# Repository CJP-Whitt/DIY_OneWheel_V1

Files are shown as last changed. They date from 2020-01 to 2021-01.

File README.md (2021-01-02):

# DIY OneWheel
Custom DIY OneWheel Electric Board. I decided to try to make an easy to follow guide on my one wheel process in hopes that everyone else doesn't have to go through the same pain as me in order to do their own DIY OneWheel. Very fun project with great opportunities for learning to engineer.

Link to the CAD File --> https://a360.co/2GcbuvP

# Disclaimer!
Do your research! I do not take responsibility for any issues you may encounter during your build if you attempt to make a onewheel. It is difficult and there are many roadblocks you must engineer your way through. Learning comes through failure and troubleshooting so get used to it now if you plan on doing more projects in the future.

# Finished Project
### _Max Range: 5.5 miles (8.8 km), Max Speed: 20mph (32 kmh)_
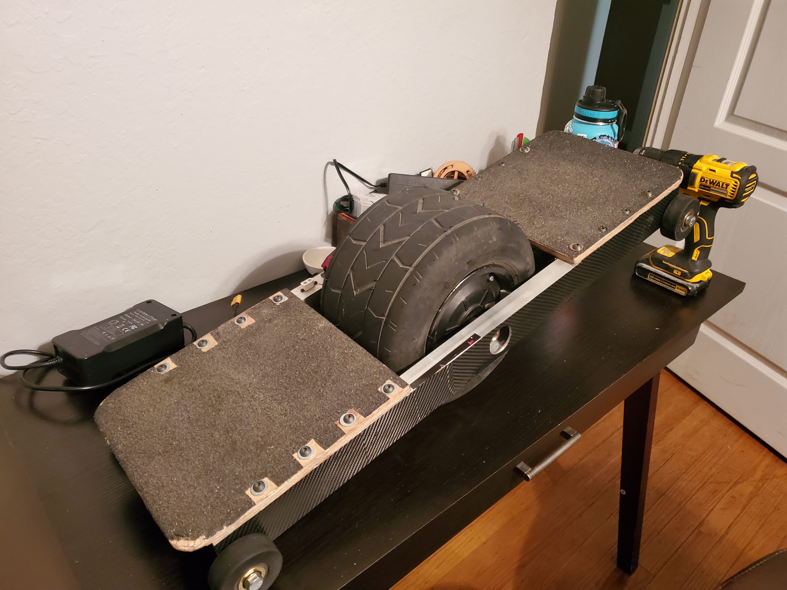
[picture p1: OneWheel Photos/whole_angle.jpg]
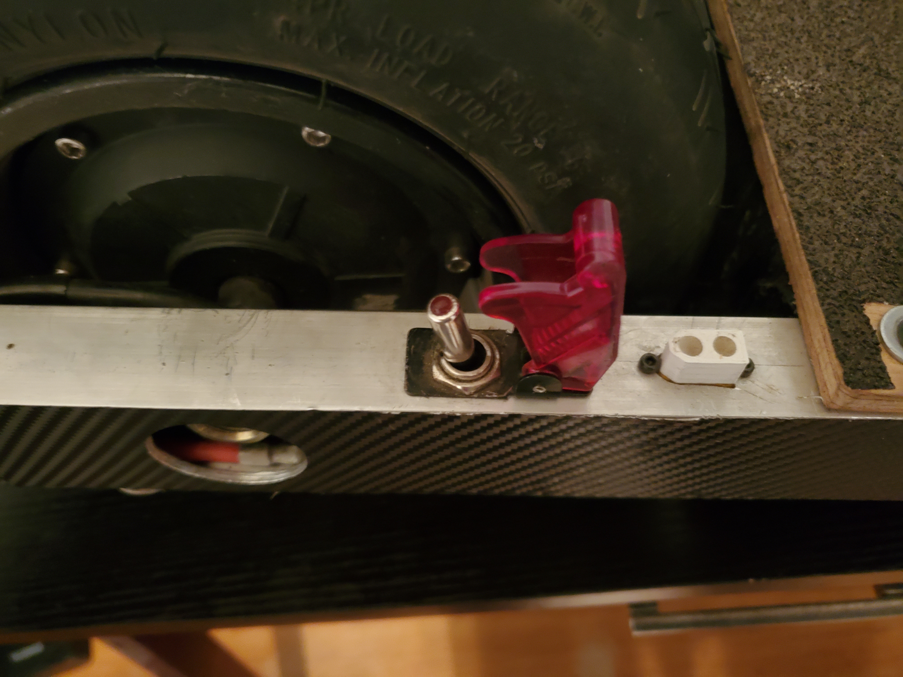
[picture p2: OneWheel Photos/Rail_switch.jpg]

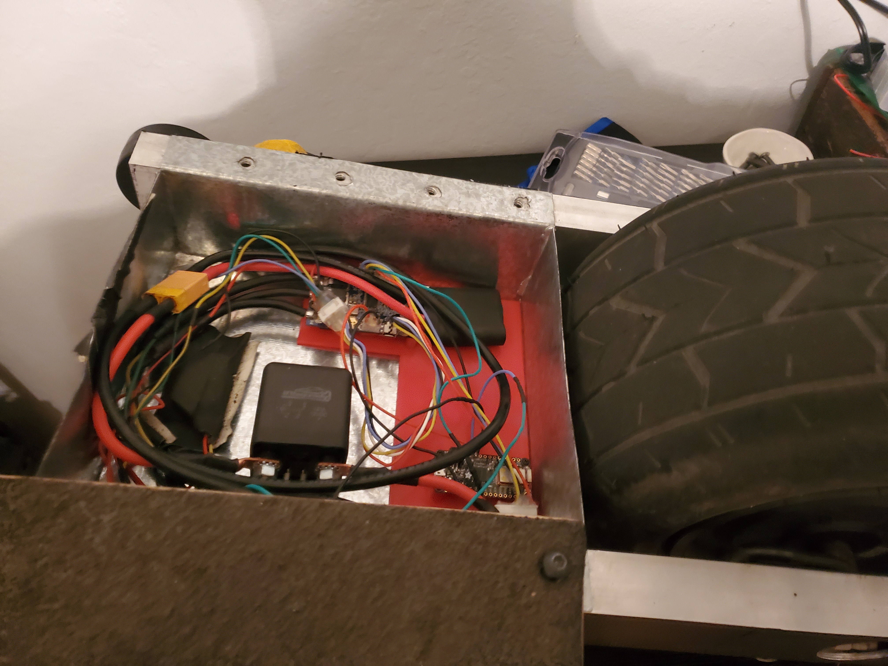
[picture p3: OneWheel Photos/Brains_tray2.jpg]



# Components
**Fundamental Components**
1. MPU6050 gyro, you can get these anywhere.
2. TORQUE ESC BLDC ELECTRONIC SPEED CONTROLLER (VESC-Motor Controller): https://diyelectricskateboard.com/products/torque-esc-bldc-electronic-speed-controller
3. 10inch 10 inch 10x6.00-5.5 wide tubeless tyre brushless gearless dc wheel hub motor (600W, 48V): https://www.aliexpress.com/item/32823573279.html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,searchweb201602_10,searchweb201603_55
4. Grip Tape (Get this anywhere that fits and has good reviews)
5. 13 18650 3.7 single cell batteries: (Get this anywhere, preferably samsung brand)
6. 48V 13s Battery Management System (BMS): https://vruzend.com/product/48v-13s-battery-management-system-bms/
7. VRUZEND battery kit V2.1 (Battery Clips): https://vruzend.com/product/vruzend-battery-kit-v2-0/
8. Relay 12v switch, 120A max (really only needs to be more Amps rating than your fuse by a little): https://www.amazon.com/Heavy-Duty-Relay-Split-Charge/dp/B07T35K8S2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
9. 60v to 3v-32v step-down converter, preferably one with a flyback diode, you can get them everywhere and I got one on ebay

**Other Components**
1. Pressure-Sensitive Conductive Sheet: https://www.adafruit.com/product/1361
2. Aluminum Rectangular Hollow Tube 2" x 1" https://store.buymetal.com/aluminum/rectangular-tube/6061-t6-t6511/aluminum-rectangular-tube-6061-t6511-2-1-0.125.html
3. Switch, I used an aircraft style switch because they look cool...but any will work as long as it works with the output voltage of your voltage step-down converter. In my case it was 12v
4. If you are doing the arduino method you need another voltage step-down from 48ish volts to 5v to power your arduino board
5. I suggest using JST Connectors!!! It's super cheap to get on Amazon and will help you undo your mistakes much easier
6. Rubber wheels with bearing: https://www.mcmaster.com/catalog/126/1524

# Build Info
- 48v 13s 2p Battery Pack
- (Easy) Vesc open source balancing tool
- (Hard) Arduino self made balancing logic

# Build Progression

### Step One: The frame
I have created a CAD file (Uses Fusion 360 which is FREE!) for the frame if you want to follow my process, but generally you need two rails that will hold the wires going from the battery compartment to your other component and mounts for connecting the motor axle to your rails. If you are a machinist this will be fairly easy, but if not I suggest you have someone else do this part. My CAD files provide the general outline but you need to decide how you want to do your own motor mounts. The third pic is after I finished and put my switch and stuff in. The yellow male connector is wired for charging to the bms and pack.
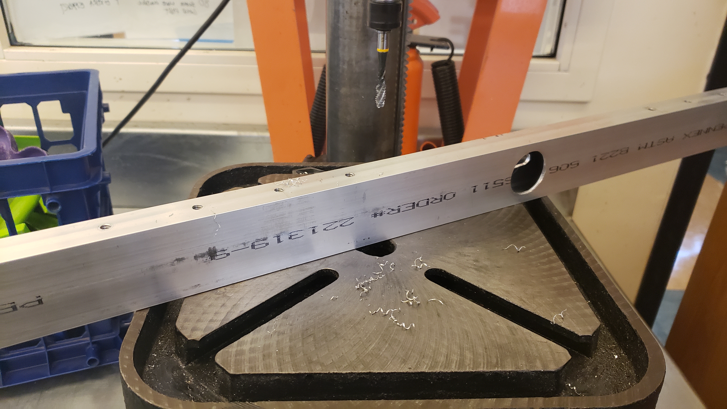
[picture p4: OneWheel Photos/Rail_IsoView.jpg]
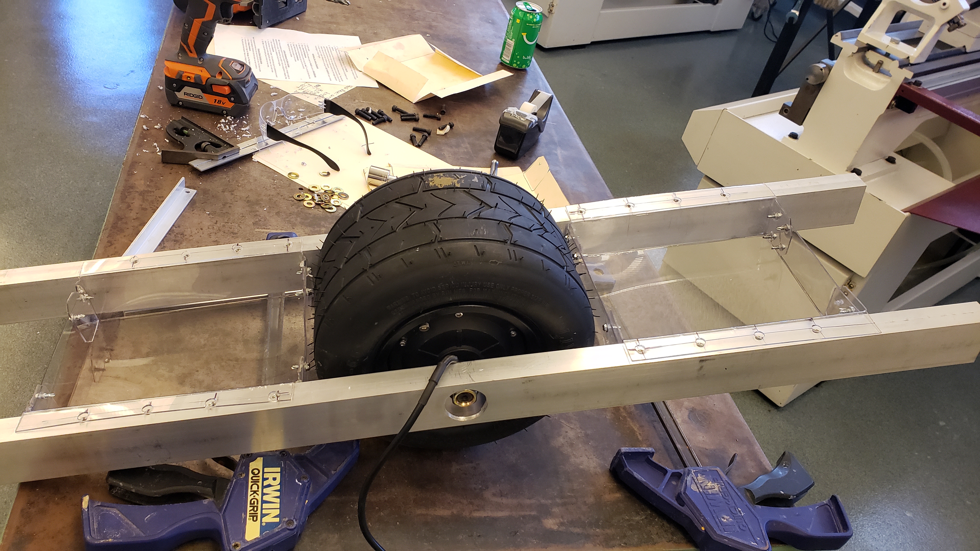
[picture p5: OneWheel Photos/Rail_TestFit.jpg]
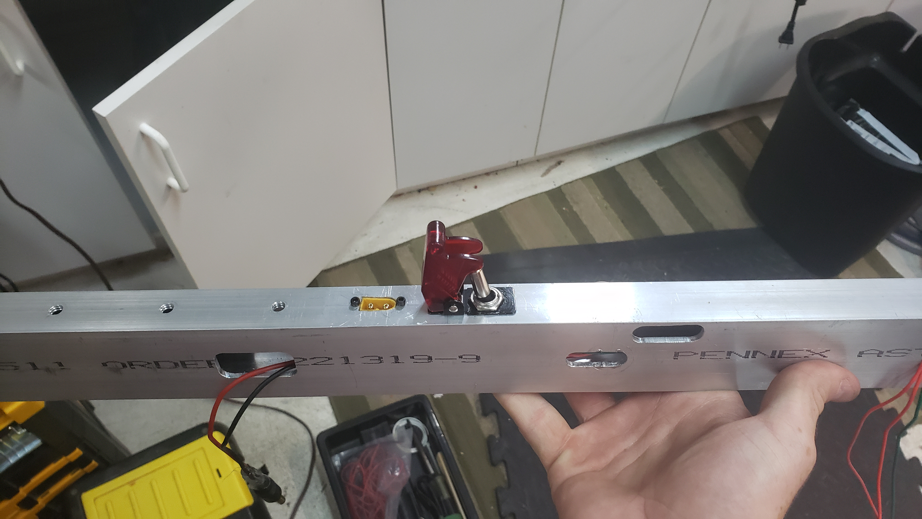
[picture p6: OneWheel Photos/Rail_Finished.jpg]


- Two rails
- Motor mounts: I attached straight to rails with a slot lock washer that comes with the wheel. Did not hold up very long : ( 
- Holes on top of rails to attach component trays and foot pads
- I would suggest getting the rails extra long just in case you need larger component trays than you first thought, you can cut them later

The Aluminum was too weak to support the motor axle twisting back and forth constantly so I made some L shaped steel brackets with a slot in the middle for the axle. I don't have any pics of them when I was working on them but here you can see them on the rails.
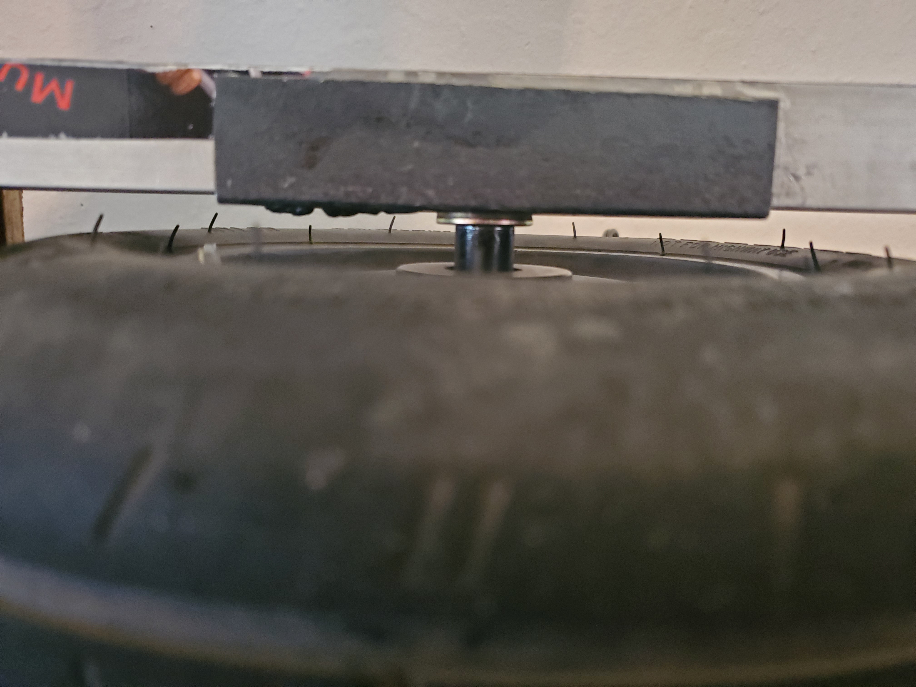
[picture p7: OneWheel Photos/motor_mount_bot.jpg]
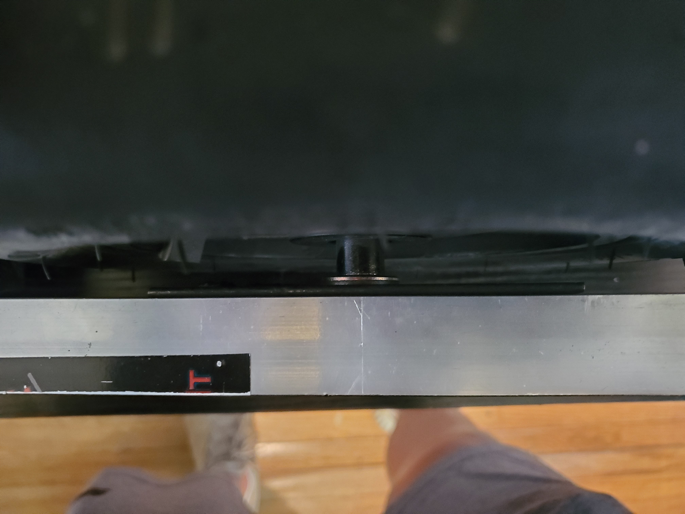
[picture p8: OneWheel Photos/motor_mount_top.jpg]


### Step Two: Battery Pack
I would suggest that if you are unfamiliar with batteries you do some research prior to building your packs. Essentially I built two 13 cell packs and ran them parallel, but it's not apparent from my final photo because I did some wiring magic to make more space in my battery tray.
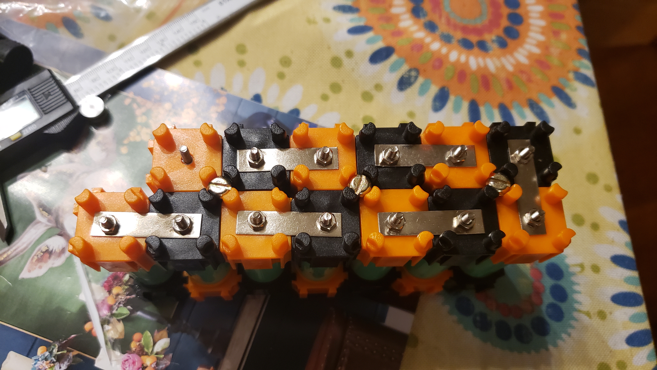
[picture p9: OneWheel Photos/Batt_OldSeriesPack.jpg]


- 26 18650 3.7 cells total
- 13 cells in series (x2)
- Put both those packs in parallel
- (You could do this with 13 cells and just make one pack if you really want, it will have the same voltage, but I wanted more amp-hours)
- Look at the wiring guide for your battery management system (BMS) and wire accordingly. In my case I soldered 1 balancing wire to each two cell groups for a total of 13 wires. Then I connected the + and - wires to their respective locations. This video helped me a lot: https://www.youtube.com/watch?v=m4DGDkwFr54

### Step Three: Component Wiring
At this point in the project I 3D printed two trays to hold my batteries and components. I also printed a plate to hold all of my non battery components, all these components are in the OneWheel frame CAD file.
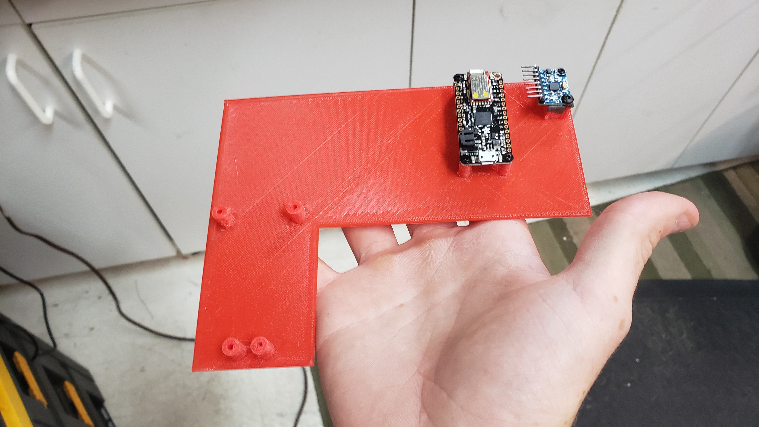
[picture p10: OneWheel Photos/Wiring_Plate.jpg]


Here is a general wiring diagram for the OneWheel. Sorry for how unprofessional it is. Keep in mind if you are using something besides the VESC balancing app you need to wire the arduino board or whatever you use for the balancing logic in between the vesc and relay.
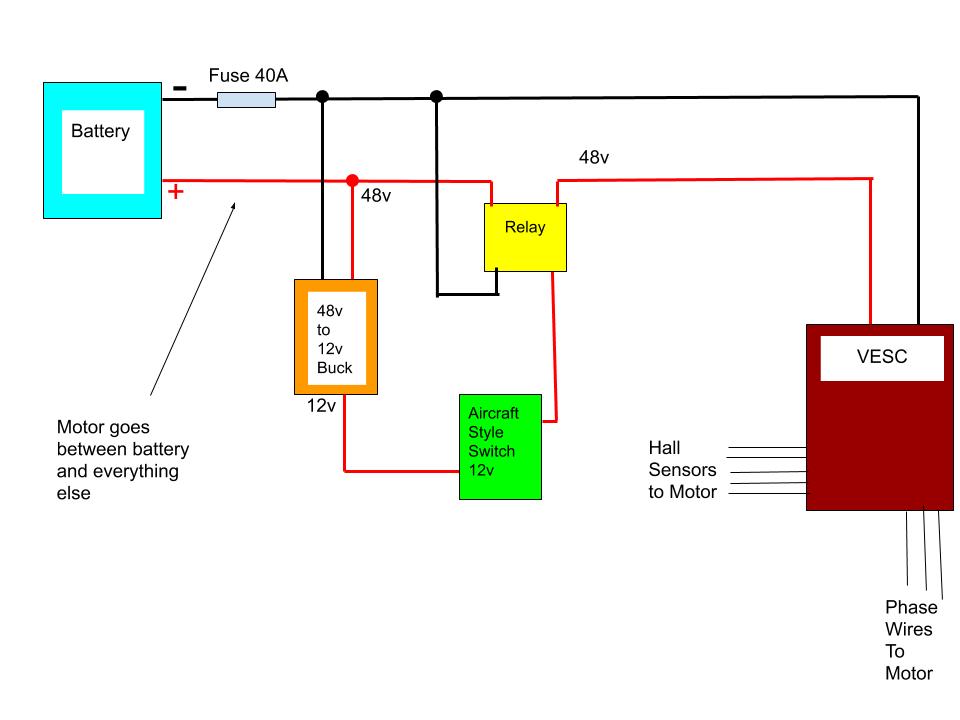
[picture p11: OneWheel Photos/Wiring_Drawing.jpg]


This is the adjustable voltage step down converter I used
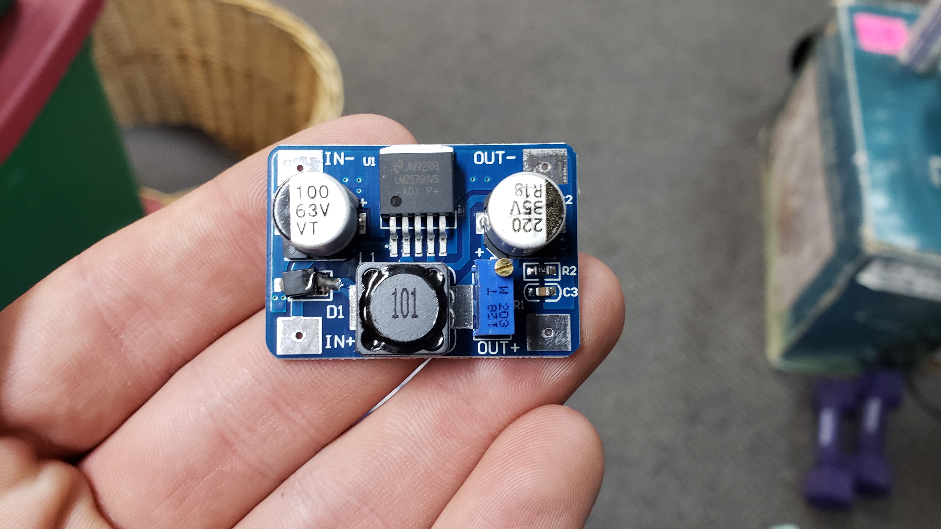
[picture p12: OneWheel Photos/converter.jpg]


Here is a photo of the hall sensor connection to the VESC, from left to right in the pic it goes 5v,Temp,H3,H2,H1,GND
I'm pretty sure the order of hall sensors doesn't matter, if it doesn't work in vesc than just switch two and it should.
Same goes for the phase wires (The 3 bullet connectors coming from the motor).
The motor listed in the parts section does not have a temp wire so leave that pin empty.
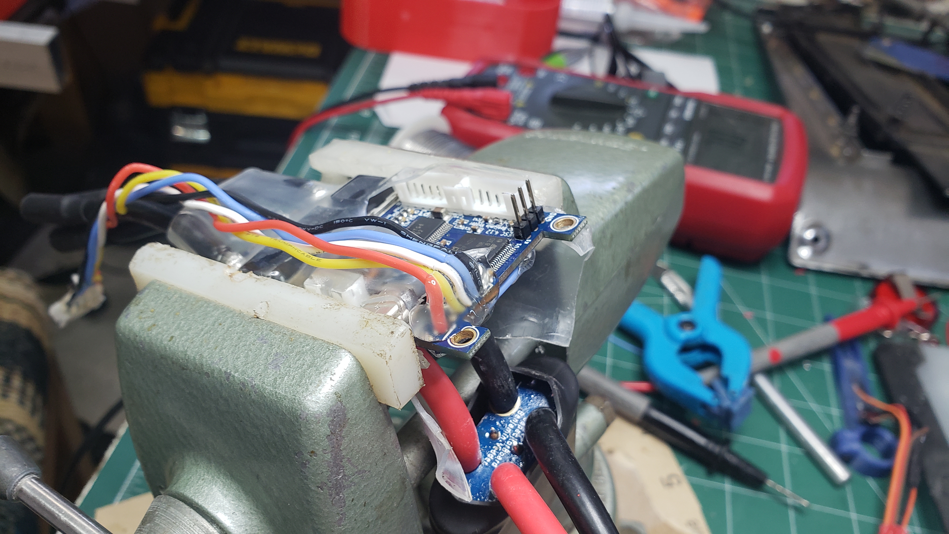
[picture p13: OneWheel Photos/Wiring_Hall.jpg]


This is the wiring for the MPU6050...
alt test

And its connection to the VESC, it's the connector at the front of the picture.
The wires you don't see in the MPU (Dark Blue, two greens) are the wires for the switches, which will be wired to footpads later, but it's best to just use them as bare wires for testing. Dark blue is the 3.3v pin, and when connected with one or both green wires (MISO, SCK) it will toggle switches on the VESC we will use later.
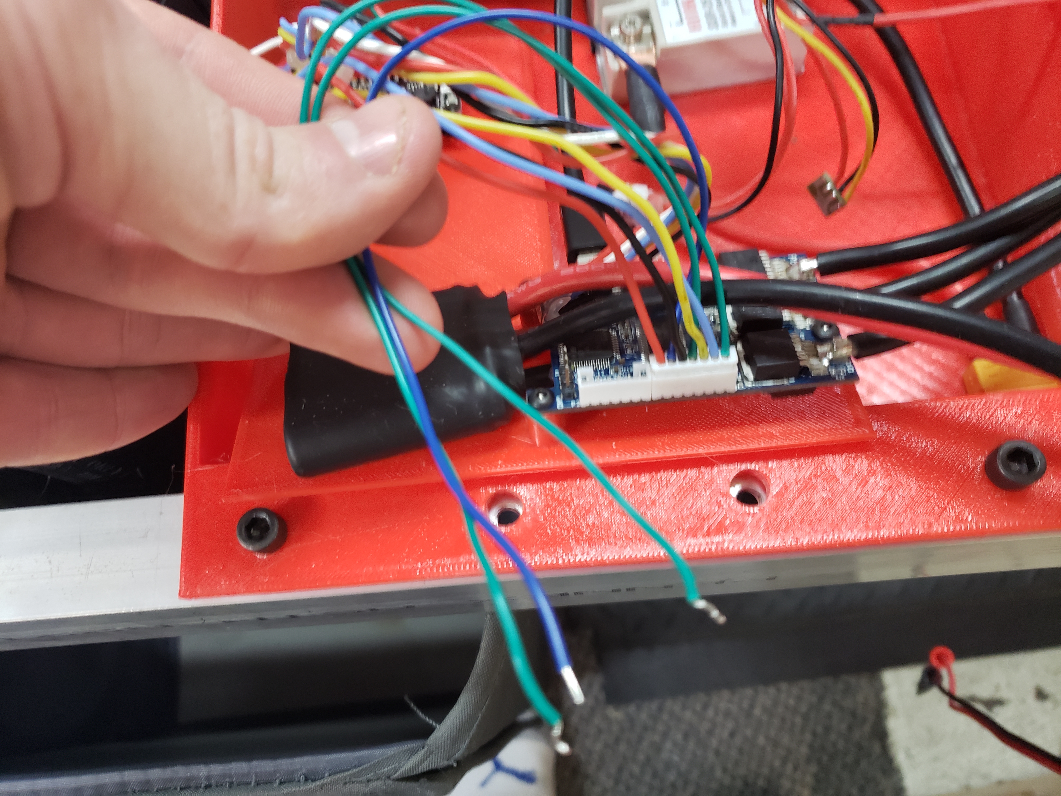
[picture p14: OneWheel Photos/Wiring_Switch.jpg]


#### Finished Component and Battery Tray
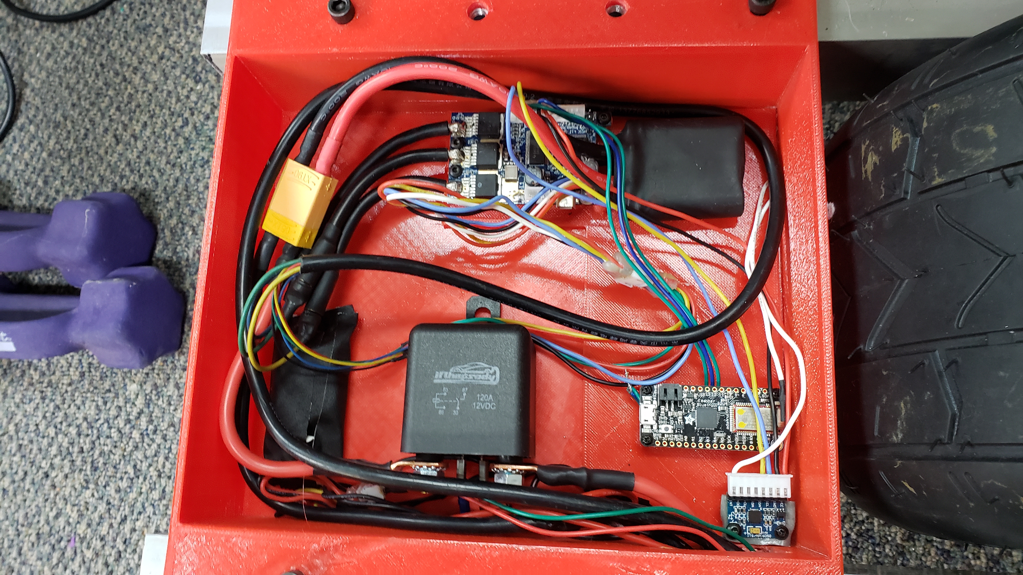
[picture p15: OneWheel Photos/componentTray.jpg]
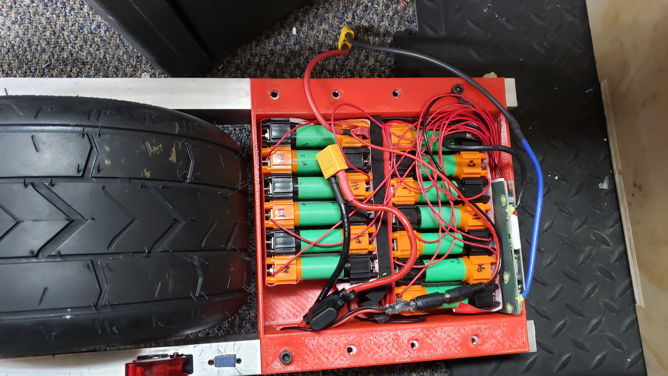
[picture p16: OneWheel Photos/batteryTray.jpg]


### Step Four: Metal Trays
The 3D printed trays were not holding up in early tests so I made some metal trays out of very thin steel sheet metal.
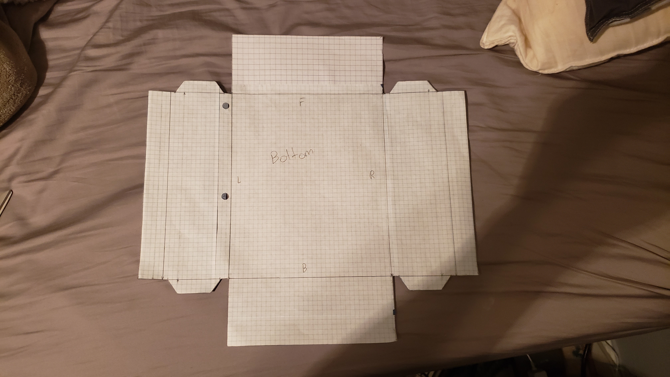
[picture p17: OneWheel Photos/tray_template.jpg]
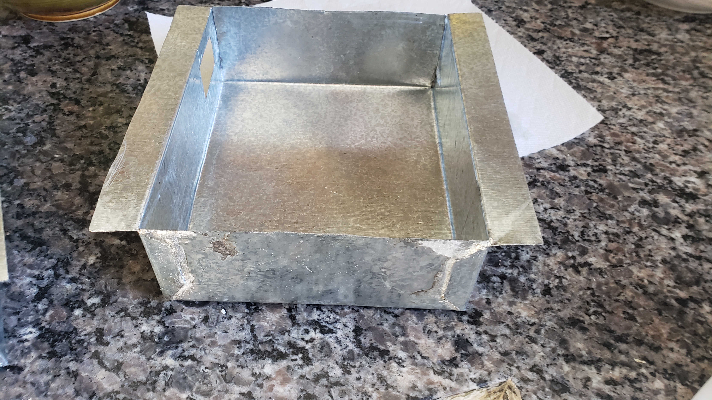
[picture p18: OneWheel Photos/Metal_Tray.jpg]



### Step Five: VESC App
With everything now wired up I would suggest you test using a multimeter from the beginning of your wiring to the end to make sure you don't fry anything. This is also why I say to use a fuse.

Plug in your vesc and open the app (Google how to get the app, it's easy). Then turn on your OneWheel
Here is a good video on how to set it all up: https://www.youtube.com/watch?v=0y5ME2SgwLg

I have XML files for the settings of the motor and app configuration in this repo

After this you can technically ride it fairly easily but it will only go 12mph so I went ahead and added some other stuff to make the ride better.

### Safety Wheels
I bought some rubber wheels with bearings from McMaster-Carr but sadly I measured something wrong and they didn't fit inside the rails, so I attached them on the outer side of the rail, with the bolt going through a hole on the other side for rigidity.

Here they are attached to the side of the rails
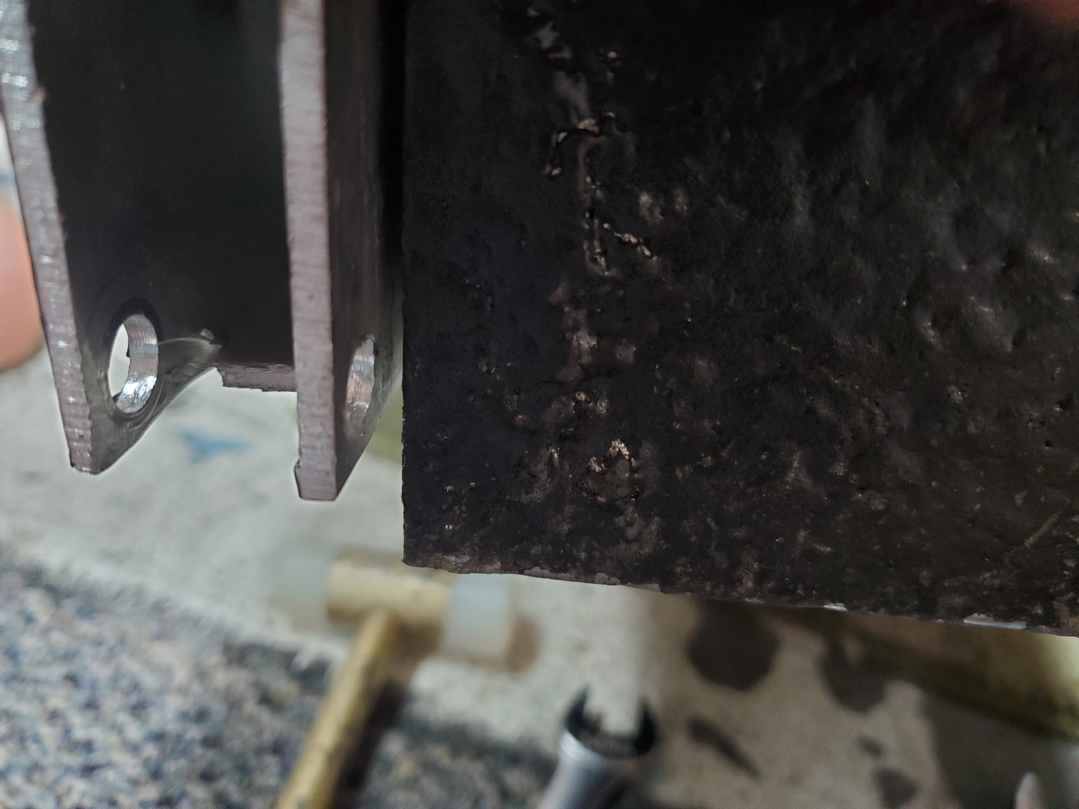
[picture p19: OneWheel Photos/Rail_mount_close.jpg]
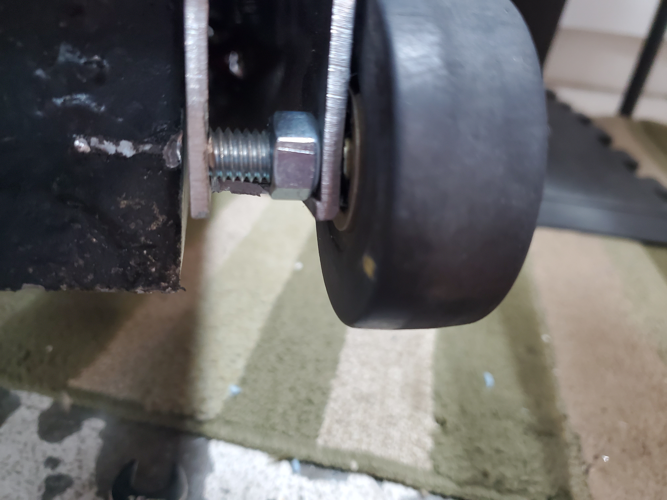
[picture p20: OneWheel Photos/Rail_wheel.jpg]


### Motor Modification
So this motor comes stock wired in the “wye”(star) configuration which for bldc motors means high torque low rpm. So after getting advice from others I went ahead and wired the motor to be in the “delta” configuration. This enabled me to reach speeds of 20mph, but with roughly 70% less torque so less acceleration. But for me as a 190 lb dude I can still ride it with ease.

For great info on this read up: https://forum.esk8.news/t/redstar-diy-onewheel/10595/73
Also this video helped me, it’s basically the conversion but in reverse: https://www.youtube.com/watch?v=b7DkOYdarkU

Here's some pics of my process…
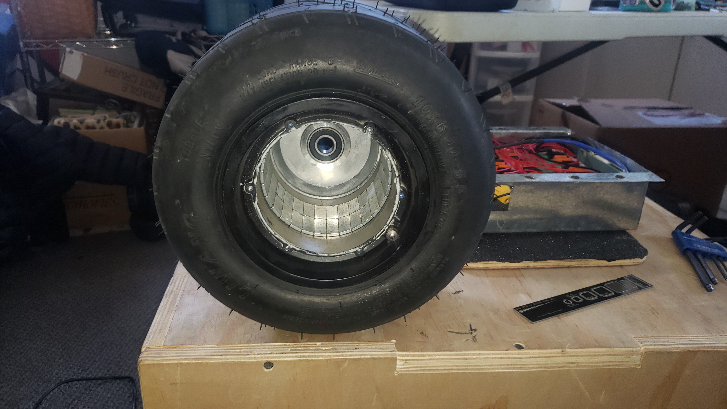
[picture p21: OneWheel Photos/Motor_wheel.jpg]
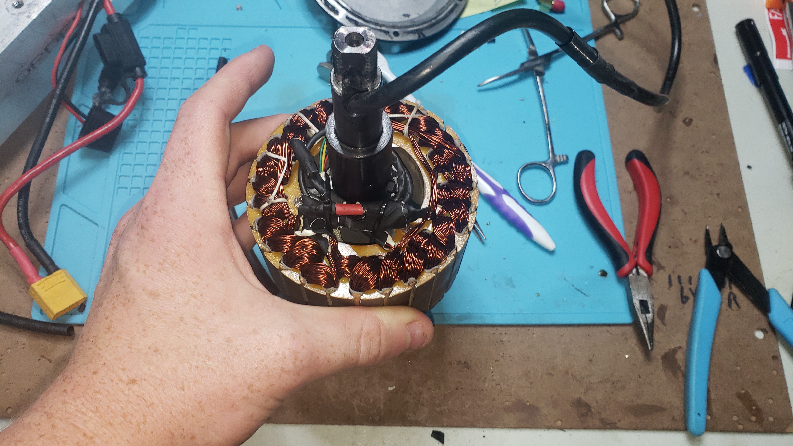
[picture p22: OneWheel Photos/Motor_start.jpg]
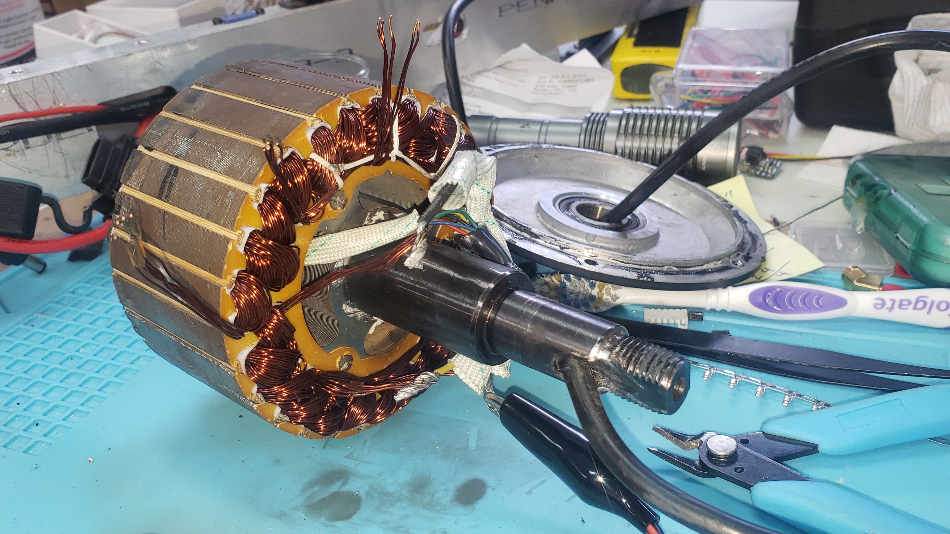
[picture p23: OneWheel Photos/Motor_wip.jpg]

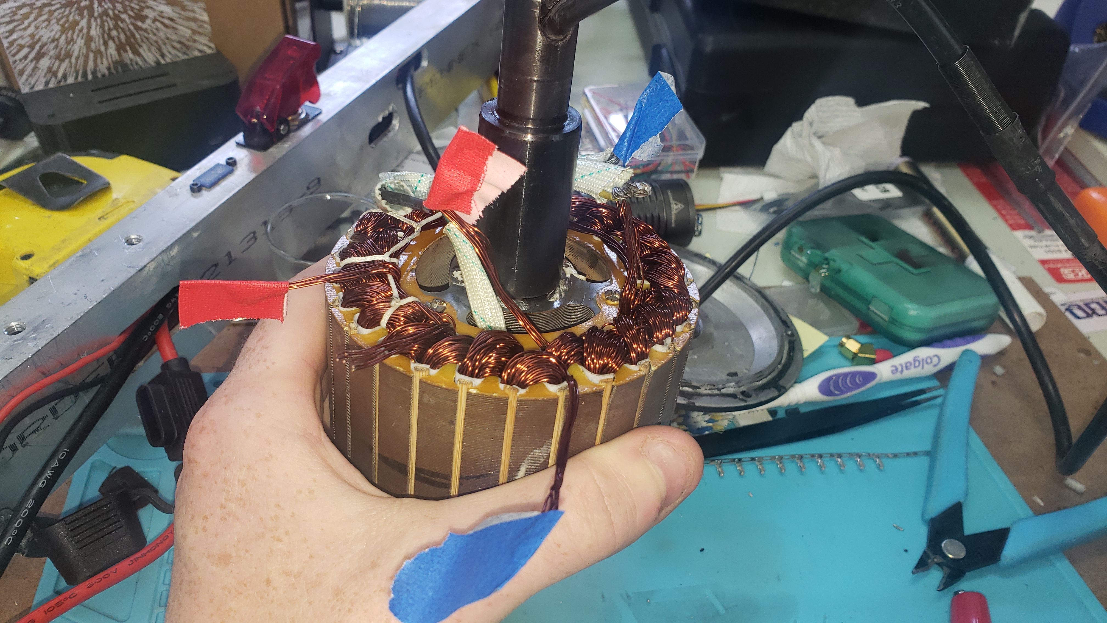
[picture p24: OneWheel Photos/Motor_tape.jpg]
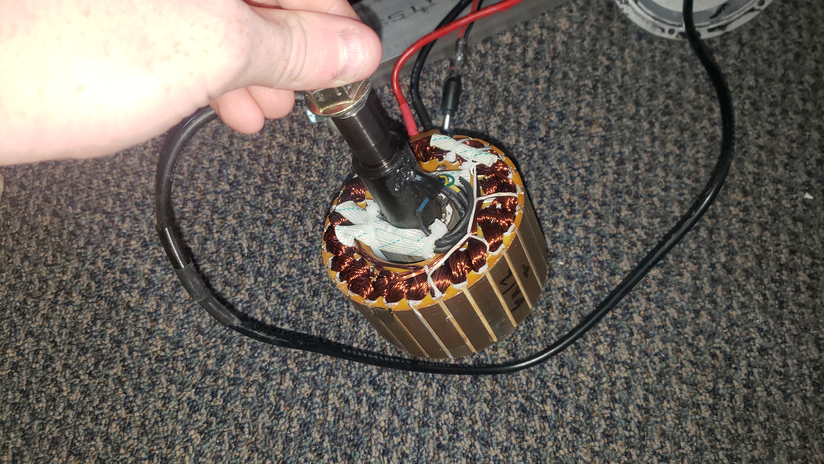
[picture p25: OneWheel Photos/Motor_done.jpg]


### Footpads
I really thought this would be the easiest part but it ended up taking much longer than I wanted. I couldn't get the built in footpad sensing in the VESC app to work with my velostat, I think it may have been because my velostat was barely changing the voltage. So I used a small arduino board to do the footpad logic and then feed that to the VESC.

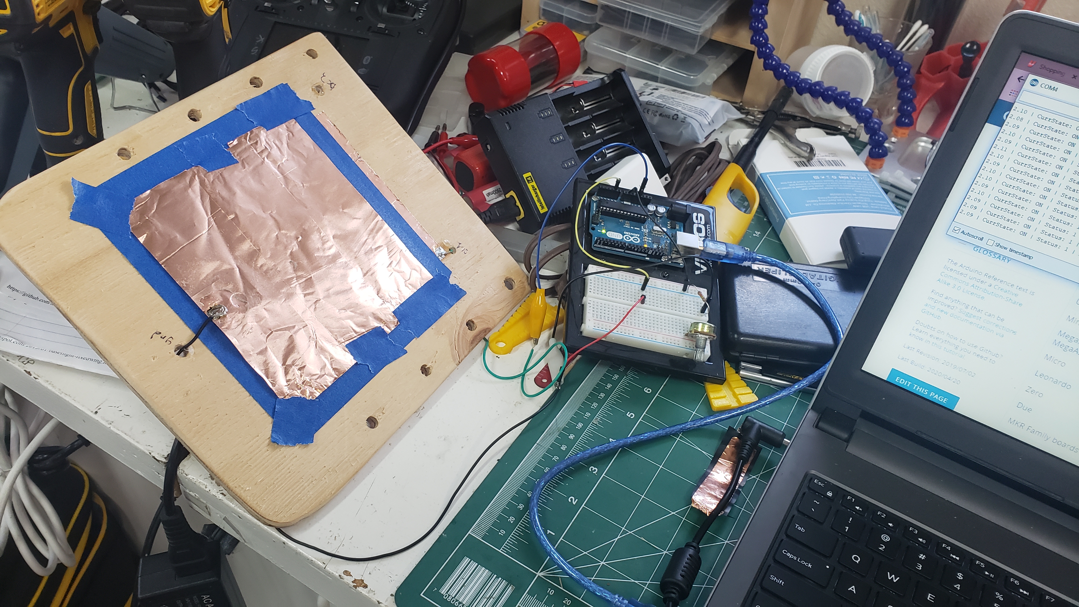
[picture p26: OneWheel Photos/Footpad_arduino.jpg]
 


I powered the arduino off of the 5v and GND from the CAN-BUS port on the VESC

Arduino code is in this repo

## Demos



### Maiden Voyage
-First time testing the OneWheel --> https://www.youtube.com/watch?v=Fk23jWkvQ68

-First good rides --> https://youtu.be/yCfcjczSD3g  |  https://youtu.be/kdDiJmPOgKU 

## Future Plans
1. Added parallel pack to fit in the brains tray
2. More compact battery packs so I can shrink tray depth
3. More concealed wheels

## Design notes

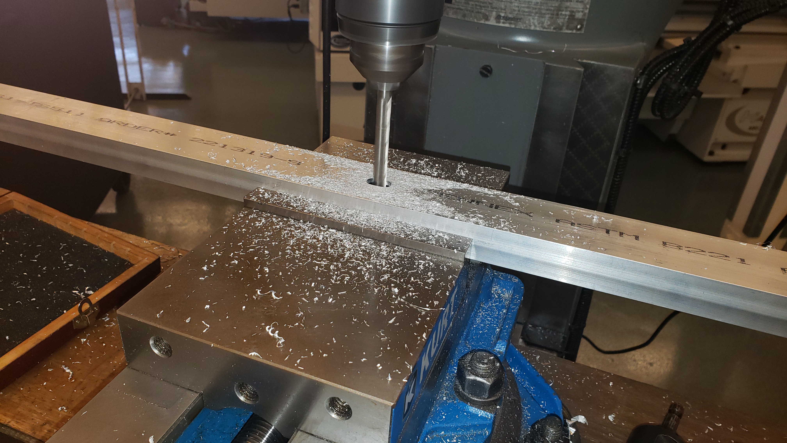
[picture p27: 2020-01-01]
OneWheel Photos/Rail_Slot.jpg

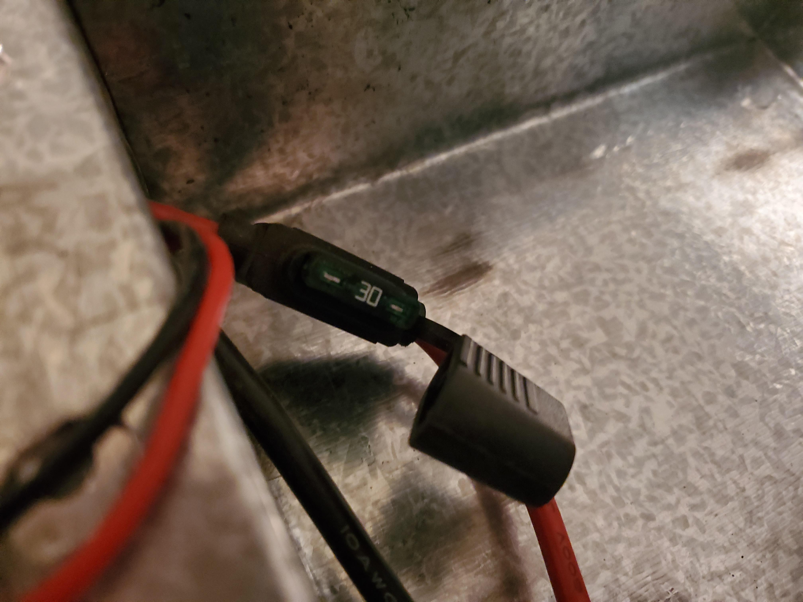
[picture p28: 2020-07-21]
OneWheel Photos/fuse.jpg

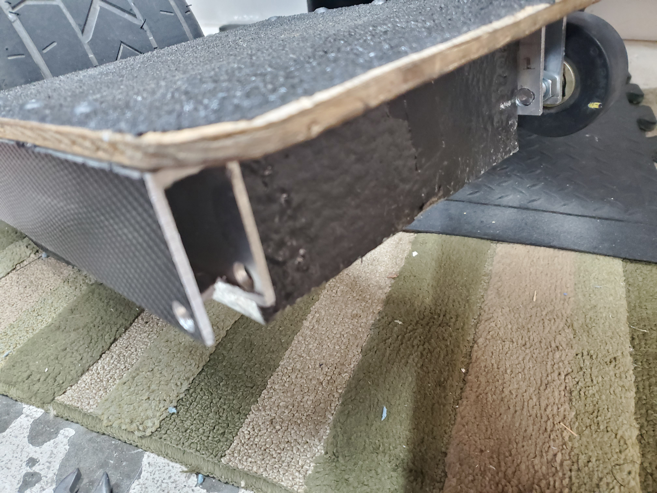
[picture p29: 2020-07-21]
OneWheel Photos/Rail_mount.jpg

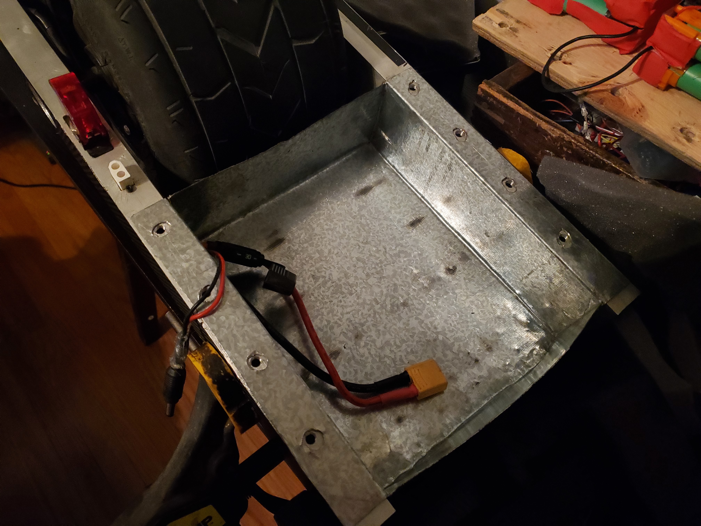
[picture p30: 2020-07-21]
OneWheel Photos/battery_tray_wide.jpg

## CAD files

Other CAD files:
DIY_OneWheel_Frame.f3z

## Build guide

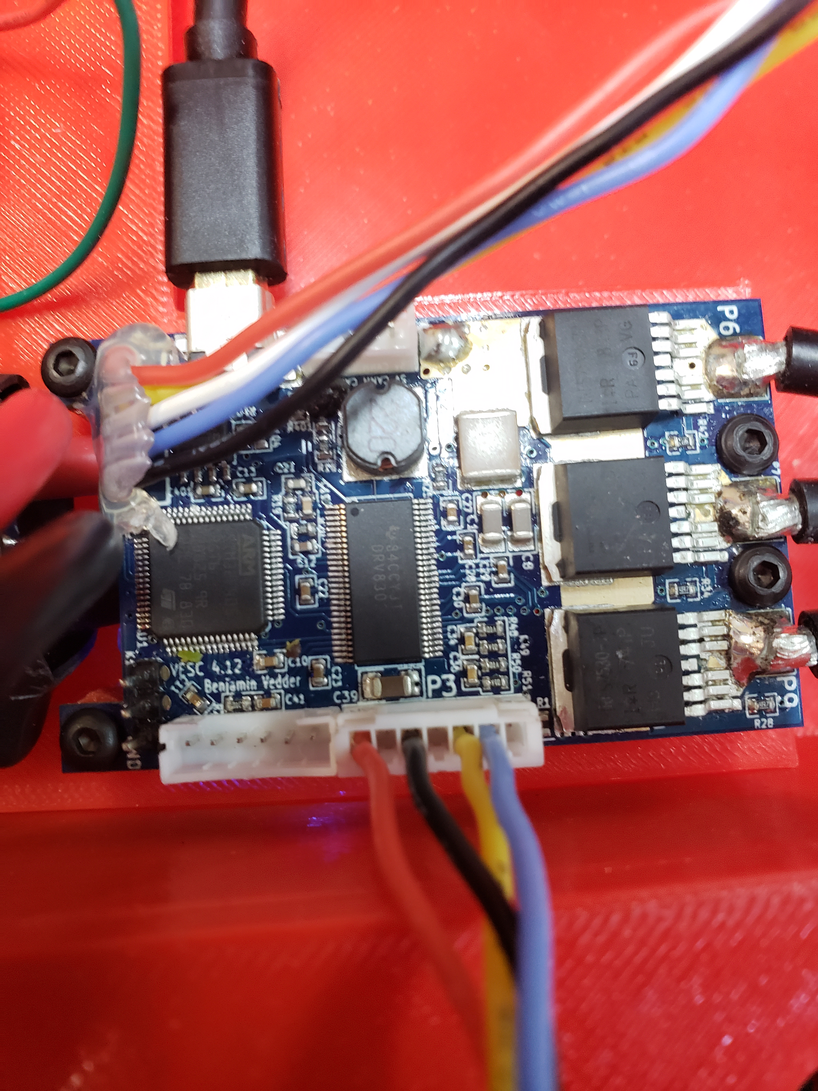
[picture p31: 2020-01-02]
OneWheel Photos/Wiring_VescMPU.jpg

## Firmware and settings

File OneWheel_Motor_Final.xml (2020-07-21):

<?xml version="1.0" encoding="UTF-8"?>
<MCConfiguration>
    <pwm_mode>1</pwm_mode>
    <comm_mode>0</comm_mode>
    <motor_type>2</motor_type>
    <sensor_mode>0</sensor_mode>
    <l_current_max>50</l_current_max>
    <l_current_min>-50</l_current_min>
    <l_in_current_max>20</l_in_current_max>
    <l_in_current_min>-15</l_in_current_min>
    <l_abs_current_max>130</l_abs_current_max>
    <l_min_erpm>-100000</l_min_erpm>
    <l_max_erpm>100000</l_max_erpm>
    <l_erpm_start>0.95</l_erpm_start>
    <l_max_erpm_fbrake>300</l_max_erpm_fbrake>
    <l_max_erpm_fbrake_cc>1500</l_max_erpm_fbrake_cc>
    <l_min_vin>8</l_min_vin>
    <l_max_vin>57</l_max_vin>
    <l_battery_cut_start>44.2</l_battery_cut_start>
    <l_battery_cut_end>39</l_battery_cut_end>
    <l_slow_abs_current>1</l_slow_abs_current>
    <l_temp_fet_start>85</l_temp_fet_start>
    <l_temp_fet_end>100</l_temp_fet_end>
    <l_temp_motor_start>85</l_temp_motor_start>
    <l_temp_motor_end>100</l_temp_motor_end>
    <l_temp_accel_dec>0.15</l_temp_accel_dec>
    <l_min_duty>0.005</l_min_duty>
    <l_max_duty>0.95</l_max_duty>
    <l_watt_max>1.5e+06</l_watt_max>
    <l_watt_min>-1.5e+06</l_watt_min>
    <l_current_max_scale>1</l_current_max_scale>
    <l_current_min_scale>1</l_current_min_scale>
    <l_duty_start>1</l_duty_start>
    <sl_min_erpm>150</sl_min_erpm>
    <sl_min_erpm_cycle_int_limit>1100</sl_min_erpm_cycle_int_limit>
    <sl_max_fullbreak_current_dir_change>10</sl_max_fullbreak_current_dir_change>
    <sl_cycle_int_limit>810.29</sl_cycle_int_limit>
    <sl_phase_advance_at_br>0.8</sl_phase_advance_at_br>
    <sl_cycle_int_rpm_br>80000</sl_cycle_int_rpm_br>
    <sl_bemf_coupling_k>900</sl_bemf_coupling_k>
    <hall_table__0>6</hall_table__0>
    <hall_table__1>6</hall_table__1>
    <hall_table__2>2</hall_table__2>
    <hall_table__3>1</hall_table__3>
    <hall_table__4>4</hall_table__4>
    <hall_table__5>5</hall_table__5>
    <hall_table__6>3</hall_table__6>
    <hall_table__7>6</hall_table__7>
    <hall_sl_erpm>2000</hall_sl_erpm>
    <foc_current_kp>0.1071</foc_current_kp>
    <foc_current_ki>63.24</foc_current_ki>
    <foc_f_sw>20000</foc_f_sw>
    <foc_dt_us>0.08</foc_dt_us>
    <foc_encoder_inverted>0</foc_encoder_inverted>
    <foc_encoder_offset>180</foc_encoder_offset>
    <foc_encoder_ratio>7</foc_encoder_ratio>
    <foc_encoder_sin_gain>1</foc_encoder_sin_gain>
    <foc_encoder_cos_gain>1</foc_encoder_cos_gain>
    <foc_encoder_sin_offset>1.65</foc_encoder_sin_offset>
    <foc_encoder_cos_offset>1.65</foc_encoder_cos_offset>
    <foc_encoder_sincos_filter_constant>0.5</foc_encoder_sincos_filter_constant>
    <foc_sensor_mode>2</foc_sensor_mode>
    <foc_pll_kp>2000</foc_pll_kp>
    <foc_pll_ki>30000</foc_pll_ki>
    <foc_motor_l>0.00010706</foc_motor_l>
    <foc_motor_r>0.0632</foc_motor_r>
    <foc_motor_flux_linkage>0.019478</foc_motor_flux_linkage>
    <foc_observer_gain>2.64e+06</foc_observer_gain>
    <foc_observer_gain_slow>0.3</foc_observer_gain_slow>
    <foc_duty_dowmramp_kp>10</foc_duty_dowmramp_kp>
    <foc_duty_dowmramp_ki>200</foc_duty_dowmramp_ki>
    <foc_openloop_rpm>300</foc_openloop_rpm>
    <foc_sl_openloop_hyst>0.1</foc_sl_openloop_hyst>
    <foc_sl_openloop_time>0.1</foc_sl_openloop_time>
    <foc_sl_d_current_duty>0</foc_sl_d_current_duty>
    <foc_sl_d_current_factor>0</foc_sl_d_current_factor>
    <foc_hall_table__0>255</foc_hall_table__0>
    <foc_hall_table__1>16</foc_hall_table__1>
    <foc_hall_table__2>85</foc_hall_table__2>
    <foc_hall_table__3>52</foc_hall_table__3>
    <foc_hall_table__4>151</foc_hall_table__4>
    <foc_hall_table__5>182</foc_hall_table__5>
    <foc_hall_table__6>118</foc_hall_table__6>
    <foc_hall_table__7>255</foc_hall_table__7>
    <foc_sl_erpm>3000</foc_sl_erpm>
    <foc_sample_v0_v7>0</foc_sample_v0_v7>
    <foc_sample_high_current>0</foc_sample_high_current>
    <foc_sat_comp>0</foc_sat_comp>
    <foc_temp_comp>0</foc_temp_comp>
    <foc_temp_comp_base_temp>25</foc_temp_comp_base_temp>
    <foc_current_filter_const>0.1</foc_current_filter_const>
    <foc_cc_decoupling>2</foc_cc_decoupling>
    <foc_observer_type>0</foc_observer_type>
    <foc_hfi_voltage_start>20</foc_hfi_voltage_start>
    <foc_hfi_voltage_run>4</foc_hfi_voltage_run>
    <foc_hfi_voltage_max>10</foc_hfi_voltage_max>
    <foc_sl_erpm_hfi>2000</foc_sl_erpm_hfi>
    <foc_hfi_start_samples>65</foc_hfi_start_samples>
    <foc_hfi_obs_ovr_sec>0.001</foc_hfi_obs_ovr_sec>
    <foc_hfi_samples>1</foc_hfi_samples>
    <gpd_buffer_notify_left>200</gpd_buffer_notify_left>
    <gpd_buffer_interpol>0</gpd_buffer_interpol>
    <gpd_current_filter_const>0.1</gpd_current_filter_const>
    <gpd_current_kp>0.03</gpd_current_kp>
    <gpd_current_ki>50</gpd_current_ki>
    <s_pid_kp>0.004</s_pid_kp>
    <s_pid_ki>0.004</s_pid_ki>
    <s_pid_kd>0.0001</s_pid_kd>
    <s_pid_kd_filter>0.2</s_pid_kd_filter>
    <s_pid_min_erpm>900</s_pid_min_erpm>
    <s_pid_allow_braking>1</s_pid_allow_braking>
    <p_pid_kp>0.03</p_pid_kp>
    <p_pid_ki>0</p_pid_ki>
    <p_pid_kd>0.0004</p_pid_kd>
    <p_pid_kd_filter>0.2</p_pid_kd_filter>
    <p_pid_ang_div>1</p_pid_ang_div>
    <cc_startup_boost_duty>0.01</cc_startup_boost_duty>
    <cc_min_current>0.1</cc_min_current>
    <cc_gain>0.0046</cc_gain>
    <cc_ramp_step_max>0.04</cc_ramp_step_max>
    <m_fault_stop_time_ms>500</m_fault_stop_time_ms>
    <m_duty_ramp_step>0.02</m_duty_ramp_step>
    <m_current_backoff_gain>0.5</m_current_backoff_gain>
    <m_encoder_counts>8192</m_encoder_counts>
    <m_sensor_port_mode>0</m_sensor_port_mode>
    <m_invert_direction>1</m_invert_direction>
    <m_drv8301_oc_mode>0</m_drv8301_oc_mode>
    <m_drv8301_oc_adj>16</m_drv8301_oc_adj>
    <m_bldc_f_sw_min>3000</m_bldc_f_sw_min>
    <m_bldc_f_sw_max>35000</m_bldc_f_sw_max>
    <m_dc_f_sw>25000</m_dc_f_sw>
    <m_ntc_motor_beta>3380</m_ntc_motor_beta>
    <m_out_aux_mode>0</m_out_aux_mode>
    <m_motor_temp_sens_type>0</m_motor_temp_sens_type>
    <m_ptc_motor_coeff>0.61</m_ptc_motor_coeff>
    <si_motor_poles>30</si_motor_poles>
    <si_gear_ratio>2.769</si_gear_ratio>
    <si_wheel_diameter>0.24</si_wheel_diameter>
    <si_battery_type>0</si_battery_type>
    <si_battery_cells>13</si_battery_cells>
    <si_battery_ah>5</si_battery_ah>
    <motor_brand>Unnamed</motor_brand>
    <motor_model>Not Specified</motor_model>
    <motor_weight>0</motor_weight>
    <motor_poles>14</motor_poles>
    <motor_sensor_type>0</motor_sensor_type>
    <motor_description>&lt;!DOCTYPE HTML PUBLIC &quot;-//W3C//DTD HTML 4.0//EN&quot; &quot;http://www.w3.org/TR/REC-html40/strict.dtd&quot;&gt;
&lt;html&gt;&lt;head&gt;&lt;meta name=&quot;qrichtext&quot; content=&quot;1&quot; /&gt;&lt;style type=&quot;text/css&quot;&gt;
p, li { white-space: pre-wrap; }
&lt;/style&gt;&lt;/head&gt;&lt;body style=&quot; font-family:'Roboto'; font-size:12pt; font-weight:400; font-style:normal;&quot;&gt;
&lt;p style=&quot; margin-top:0px; margin-bottom:0px; margin-left:0px; margin-right:0px; -qt-block-indent:0; text-indent:0px;&quot;&gt;A motor description can be edited here.&lt;/p&gt;&lt;/body&gt;&lt;/html&gt;</motor_description>
    <motor_loss_torque>0.03</motor_loss_torque>
    <motor_quality_bearings>0</motor_quality_bearings>
    <motor_quality_magnets>0</motor_quality_magnets>
    <motor_quality_construction>0</motor_quality_construction>
    <motor_quality_description>&lt;!DOCTYPE HTML PUBLIC &quot;-//W3C//DTD HTML 4.0//EN&quot; &quot;http://www.w3.org/TR/REC-html40/strict.dtd&quot;&gt;
&lt;html&gt;&lt;head&gt;&lt;meta name=&quot;qrichtext&quot; content=&quot;1&quot; /&gt;&lt;style type=&quot;text/css&quot;&gt;
p, li { white-space: pre-wrap; }
&lt;/style&gt;&lt;/head&gt;&lt;body style=&quot; font-family:'Roboto'; font-size:12pt; font-weight:400; font-style:normal;&quot;&gt;
&lt;p style=&quot; margin-top:0px; margin-bottom:0px; margin-left:0px; margin-right:0px; -qt-block-indent:0; text-indent:0px;&quot;&gt;Some comments about the motor quality. Images can be added as well.&lt;/p&gt;&lt;/body&gt;&lt;/html&gt;</motor_quality_description>
</MCConfiguration>

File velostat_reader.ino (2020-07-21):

//Variables for holding  virtual states
String currState = "OFF";
String prevState = "OFF";
String prevprevState = "OFF";
int state = 0; //Actual state fed to VESC
int waitTime = 500; //Time in between state checks
int count = 0; //For tracking consistency

void setup() {
  // put your setup code here, to run once:
  Serial.begin(9600);
  pinMode(A1, INPUT_PULLUP);
  digitalWrite(A1, HIGH);
}

void loop() {
  // put your main code here, to run repeatedly:
  int sensorValue = analogRead(A1);
  float voltage = sensorValue;
  Serial.print(voltage);

  //Cycle virtual states backwards
  prevprevState = prevState;
  prevState = currState;

  //Get current virtual state
  if (voltage > 28){currState = "OFF";}
  else{currState = "ON";}

  Serial.print(" | CurrState: ");
  Serial.print(currState);

  //Conditional for setting actual state to OFF
  if (currState == "OFF" && prevState == "OFF" && prevprevState == "OFF"){
    state = 0;
    count++;
  }

  //Conditional for setting actual state to ON
  if (currState == "ON" && prevState == "ON" && prevprevState == "ON"){
    state = 1;
  }

  Serial.print(" | Status: ");
  Serial.print(state);

  Serial.print(" | Fails: ");
  Serial.println(count);
  delay(waitTime);
  
}

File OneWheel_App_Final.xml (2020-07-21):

<?xml version="1.0" encoding="UTF-8"?>
<APPConfiguration>
    <controller_id>81</controller_id>
    <timeout_msec>1000</timeout_msec>
    <timeout_brake_current>0</timeout_brake_current>
    <send_can_status>4</send_can_status>
    <send_can_status_rate_hz>50</send_can_status_rate_hz>
    <can_baud_rate>2</can_baud_rate>
    <pairing_done>0</pairing_done>
    <permanent_uart_enabled>1</permanent_uart_enabled>
    <shutdown_mode>7</shutdown_mode>
    <can_mode>0</can_mode>
    <uavcan_esc_index>0</uavcan_esc_index>
    <app_to_use>9</app_to_use>
    <app_ppm_conf.ctrl_type>0</app_ppm_conf.ctrl_type>
    <app_ppm_conf.pid_max_erpm>15000</app_ppm_conf.pid_max_erpm>
    <app_ppm_conf.hyst>0.15</app_ppm_conf.hyst>
    <app_ppm_conf.pulse_start>1</app_ppm_conf.pulse_start>
    <app_ppm_conf.pulse_end>2</app_ppm_conf.pulse_end>
    <app_ppm_conf.pulse_center>1.5</app_ppm_conf.pulse_center>
    <app_ppm_conf.median_filter>1</app_ppm_conf.median_filter>
    <app_ppm_conf.safe_start>1</app_ppm_conf.safe_start>
    <app_ppm_conf.throttle_exp>0</app_ppm_conf.throttle_exp>
    <app_ppm_conf.throttle_exp_brake>0</app_ppm_conf.throttle_exp_brake>
    <app_ppm_conf.throttle_exp_mode>2</app_ppm_conf.throttle_exp_mode>
    <app_ppm_conf.ramp_time_pos>0.4</app_ppm_conf.ramp_time_pos>
    <app_ppm_conf.ramp_time_neg>0.2</app_ppm_conf.ramp_time_neg>
    <app_ppm_conf.multi_esc>1</app_ppm_conf.multi_esc>
    <app_ppm_conf.tc>0</app_ppm_conf.tc>
    <app_ppm_conf.tc_max_diff>3000</app_ppm_conf.tc_max_diff>
    <app_ppm_conf.max_erpm_for_dir>4000</app_ppm_conf.max_erpm_for_dir>
    <app_ppm_conf.smart_rev_max_duty>0.07</app_ppm_conf.smart_rev_max_duty>
    <app_ppm_conf.smart_rev_ramp_time>3</app_ppm_conf.smart_rev_ramp_time>
    <app_adc_conf.ctrl_type>0</app_adc_conf.ctrl_type>
    <app_adc_conf.hyst>0.15</app_adc_conf.hyst>
    <app_adc_conf.voltage_start>0.9</app_adc_conf.voltage_start>
    <app_adc_conf.voltage_end>3</app_adc_conf.voltage_end>
    <app_adc_conf.voltage_center>2</app_adc_conf.voltage_center>
    <app_adc_conf.voltage2_start>0.9</app_adc_conf.voltage2_start>
    <app_adc_conf.voltage2_end>3</app_adc_conf.voltage2_end>
    <app_adc_conf.use_filter>1</app_adc_conf.use_filter>
    <app_adc_conf.safe_start>1</app_adc_conf.safe_start>
    <app_adc_conf.cc_button_inverted>0</app_adc_conf.cc_button_inverted>
    <app_adc_conf.rev_button_inverted>0</app_adc_conf.rev_button_inverted>
    <app_adc_conf.voltage_inverted>0</app_adc_conf.voltage_inverted>
    <app_adc_conf.voltage2_inverted>0</app_adc_conf.voltage2_inverted>
    <app_adc_conf.throttle_exp>0</app_adc_conf.throttle_exp>
    <app_adc_conf.throttle_exp_brake>0</app_adc_conf.throttle_exp_brake>
    <app_adc_conf.throttle_exp_mode>2</app_adc_conf.throttle_exp_mode>
    <app_adc_conf.ramp_time_pos>0.3</app_adc_conf.ramp_time_pos>
    <app_adc_conf.ramp_time_neg>0.1</app_adc_conf.ramp_time_neg>
    <app_adc_conf.multi_esc>1</app_adc_conf.multi_esc>
    <app_adc_conf.tc>0</app_adc_conf.tc>
    <app_adc_conf.tc_max_diff>3000</app_adc_conf.tc_max_diff>
    <app_adc_conf.update_rate_hz>500</app_adc_conf.update_rate_hz>
    <app_uart_baudrate>115200</app_uart_baudrate>
    <app_chuk_conf.ctrl_type>1</app_chuk_conf.ctrl_type>
    <app_chuk_conf.hyst>0.15</app_chuk_conf.hyst>
    <app_chuk_conf.ramp_time_pos>0.4</app_chuk_conf.ramp_time_pos>
    <app_chuk_conf.ramp_time_neg>0.2</app_chuk_conf.ramp_time_neg>
    <app_chuk_conf.stick_erpm_per_s_in_cc>3000</app_chuk_conf.stick_erpm_per_s_in_cc>
    <app_chuk_conf.throttle_exp>0</app_chuk_conf.throttle_exp>
    <app_chuk_conf.throttle_exp_brake>0</app_chuk_conf.throttle_exp_brake>
    <app_chuk_conf.throttle_exp_mode>2</app_chuk_conf.throttle_exp_mode>
    <app_chuk_conf.multi_esc>1</app_chuk_conf.multi_esc>
    <app_chuk_conf.tc>0</app_chuk_conf.tc>
    <app_chuk_conf.tc_max_diff>3000</app_chuk_conf.tc_max_diff>
    <app_chuk_conf.use_smart_rev>1</app_chuk_conf.use_smart_rev>
    <app_chuk_conf.smart_rev_max_duty>0.07</app_chuk_conf.smart_rev_max_duty>
    <app_chuk_conf.smart_rev_ramp_time>3</app_chuk_conf.smart_rev_ramp_time>
    <app_nrf_conf.speed>1</app_nrf_conf.speed>
    <app_nrf_conf.power>3</app_nrf_conf.power>
    <app_nrf_conf.crc_type>1</app_nrf_conf.crc_type>
    <app_nrf_conf.retry_delay>0</app_nrf_conf.retry_delay>
    <app_nrf_conf.retries>3</app_nrf_conf.retries>
    <app_nrf_conf.channel>76</app_nrf_conf.channel>
    <app_nrf_conf.address__0>198</app_nrf_conf.address__0>
    <app_nrf_conf.address__1>199</app_nrf_conf.address__1>
    <app_nrf_conf.address__2>0</app_nrf_conf.address__2>
    <app_nrf_conf.send_crc_ack>1</app_nrf_conf.send_crc_ack>
    <app_balance_conf.kp>45</app_balance_conf.kp>
    <app_balance_conf.ki>0.03</app_balance_conf.ki>
    <app_balance_conf.kd>0</app_balance_conf.kd>
    <app_balance_conf.hertz>1000</app_balance_conf.hertz>
    <app_balance_conf.pitch_fault>12</app_balance_conf.pitch_fault>
    <app_balance_conf.roll_fault>35</app_balance_conf.roll_fault>
    <app_balance_conf.adc1>3</app_balance_conf.adc1>
    <app_balance_conf.adc2>0</app_balance_conf.adc2>
    <app_balance_conf.overspeed_duty>0.95</app_balance_conf.overspeed_duty>
    <app_balance_conf.tiltback_duty>0.82</app_balance_conf.tiltback_duty>
    <app_balance_conf.tiltback_angle>7.5</app_balance_conf.tiltback_angle>
    <app_balance_conf.tiltback_speed>3</app_balance_conf.tiltback_speed>
    <app_balance_conf.tiltback_high_voltage>52</app_balance_conf.tiltback_high_voltage>
    <app_balance_conf.tiltback_low_voltage>43</app_balance_conf.tiltback_low_voltage>
    <app_balance_conf.startup_pitch_tolerance>1</app_balance_conf.startup_pitch_tolerance>
    <app_balance_conf.startup_roll_tolerance>10</app_balance_conf.startup_roll_tolerance>
    <app_balance_conf.startup_speed>1</app_balance_conf.startup_speed>
    <app_balance_conf.deadzone>0</app_balance_conf.deadzone>
    <app_balance_conf.current_boost>0</app_balance_conf.current_boost>
    <app_balance_conf.multi_esc>0</app_balance_conf.multi_esc>
    <app_balance_conf.yaw_kp>0</app_balance_conf.yaw_kp>
    <app_balance_conf.yaw_ki>0</app_balance_conf.yaw_ki>
    <app_balance_conf.yaw_kd>0</app_balance_conf.yaw_kd>
    <app_balance_conf.roll_steer_kp>0</app_balance_conf.roll_steer_kp>
    <app_balance_conf.brake_current>0</app_balance_conf.brake_current>
    <app_balance_conf.overspeed_delay>200</app_balance_conf.overspeed_delay>
    <app_balance_conf.fault_delay>0</app_balance_conf.fault_delay>
    <app_balance_conf.tiltback_constant>0</app_balance_conf.tiltback_constant>
    <app_balance_conf.roll_steer_erpm_kp>0</app_balance_conf.roll_steer_erpm_kp>
    <app_balance_conf.yaw_current_clamp>0</app_balance_conf.yaw_current_clamp>
    <app_balance_conf.adc_half_fault_erpm>1000</app_balance_conf.adc_half_fault_erpm>
    <app_balance_conf.setpoint_pitch_filter>0.002</app_balance_conf.setpoint_pitch_filter>
    <app_balance_conf.setpoint_target_filter>0.75</app_balance_conf.setpoint_target_filter>
    <app_balance_conf.setpoint_clamp>12</app_balance_conf.setpoint_clamp>
    <imu_conf.type>2</imu_conf.type>
    <imu_conf.mode>1</imu_conf.mode>
    <imu_conf.sample_rate_hz>1000</imu_conf.sample_rate_hz>
    <imu_conf.accel_confidence_decay>0.03</imu_conf.accel_confidence_decay>
    <imu_conf.mahony_kp>0.9</imu_conf.mahony_kp>
    <imu_conf.mahony_ki>0.005</imu_conf.mahony_ki>
    <imu_conf.madgwick_beta>0</imu_conf.madgwick_beta>
    <imu_conf.rot_roll>0.13</imu_conf.rot_roll>
    <imu_conf.rot_pitch>4.2</imu_conf.rot_pitch>
    <imu_conf.rot_yaw>90</imu_conf.rot_yaw>
    <imu_conf.accel_offsets__0>0</imu_conf.accel_offsets__0>
    <imu_conf.accel_offsets__1>0</imu_conf.accel_offsets__1>
    <imu_conf.accel_offsets__2>0</imu_conf.accel_offsets__2>
    <imu_conf.gyro_offsets__0>-1.52</imu_conf.gyro_offsets__0>
    <imu_conf.gyro_offsets__1>-0.24</imu_conf.gyro_offsets__1>
    <imu_conf.gyro_offsets__2>0.82</imu_conf.gyro_offsets__2>
    <imu_conf.gyro_offset_comp_fact__0>0</imu_conf.gyro_offset_comp_fact__0>
    <imu_conf.gyro_offset_comp_fact__1>1</imu_conf.gyro_offset_comp_fact__1>
    <imu_conf.gyro_offset_comp_fact__2>1</imu_conf.gyro_offset_comp_fact__2>
    <imu_conf.gyro_offset_comp_clamp>5</imu_conf.gyro_offset_comp_clamp>
</APPConfiguration>

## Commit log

2020-01-01 OneWheel CAD Frame
    Fusion 360 Archive file, its free just get it
    [DIY_OneWheel_Frame.f3z]
2020-01-21 Dynamic link added
    [DIY_OneWheel_Frame.f3z]
2020-07-21 Final Motor and App Config files
    These can be downloaded and opened in the VESC App to copy my settings
    [OneWheel_App_Final.xml, OneWheel_Motor_Final.xml]
2020-07-21 Arduino code for foot-pad sensing
    Code feeds actual foot-pad state data to vesc through switch wires.
